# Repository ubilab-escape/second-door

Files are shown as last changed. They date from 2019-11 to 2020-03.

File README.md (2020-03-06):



**More notes on the implementation can be seen [here](
https://github.com/ubilab-escape/second-door/blob/master/docu/implementation.md)**

# Overview

- [Riddles](#Riddles)
  * [Stage 1 - Breaking the lock of the fusebox](#stage-1---breaking-the-lock-of-the-fusebox)
  * [Stage 2 - Restoring the power supply for the robot](#stage-2---restoring-the-power-supply-for-the-robot)
  * [Stage 3 - Breaking door by robot](#stage-3---breaking-door-by-robot)
- [Communication](#Communication)
- [How to](#How-to)
- [Future work](#future-work)

# Riddles

The main concept is visualized in the figure below.

<p align="center"> 
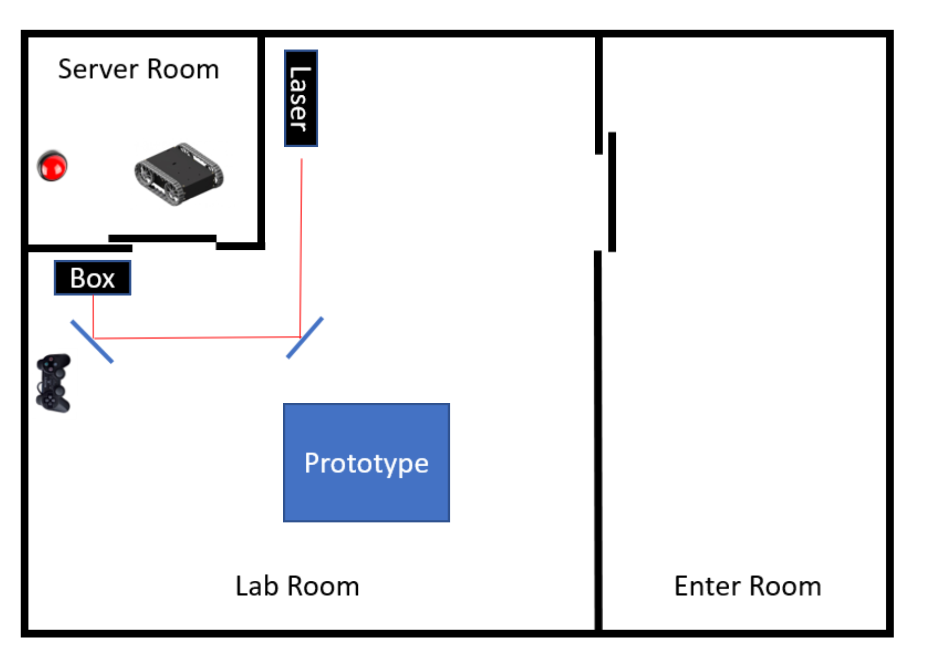
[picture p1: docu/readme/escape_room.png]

</p>
<p align="center">Figure 1: Main concept<p align="center">

To open the second door, 3 puzzles must be solved. These puzzles are called Stages in the following. In case the participants get stuck they can ask for hints. The implemented hints can be seen [here](/docu/hints.md)

## Stage 1 - Breaking the lock of the fusebox

In the first stage the group has to crack the lock of the fusebox. A laser somewhere in the room is to be used. There is a lock on the fusebox which can only be opened when the laser beam is aimed at it. To do this, the group must use mirrors to divert the laser beam through the entire room. The 2 mirrors that can be used are mounted on a wall. This hides them, and the group must come up with the idea of using the mirrors.

The lock on the fusebox measures the laser beam. So that only this specific laser light can open the lock. The readout of the signal is done by the ESP32 inside the fusebox. The progress of this crack process is visualized with LEDs arranged in a circle. Once this color circle is closed, the microcontroller gives a signal to an actuator so that the lid of the fusebox opens. This completes the first stage.

<p align="center"> 
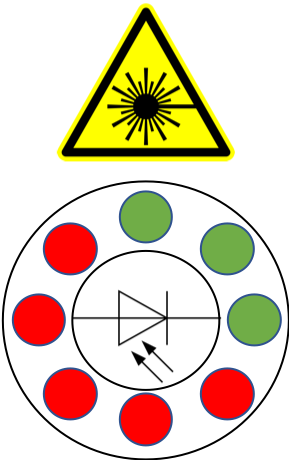
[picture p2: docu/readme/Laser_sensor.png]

</p>
<p align="center">Figure 2: Laser lock<p align="center">

To make it easier for the participants the laser warning symbol will be attached to the fusebox.

## Stage 2 - Restoring the power supply for the robot

Inside the fusebox two small "rewiring" riddles need to be solved . The following image shows the inside of the fusebox.

<p align="center"> 
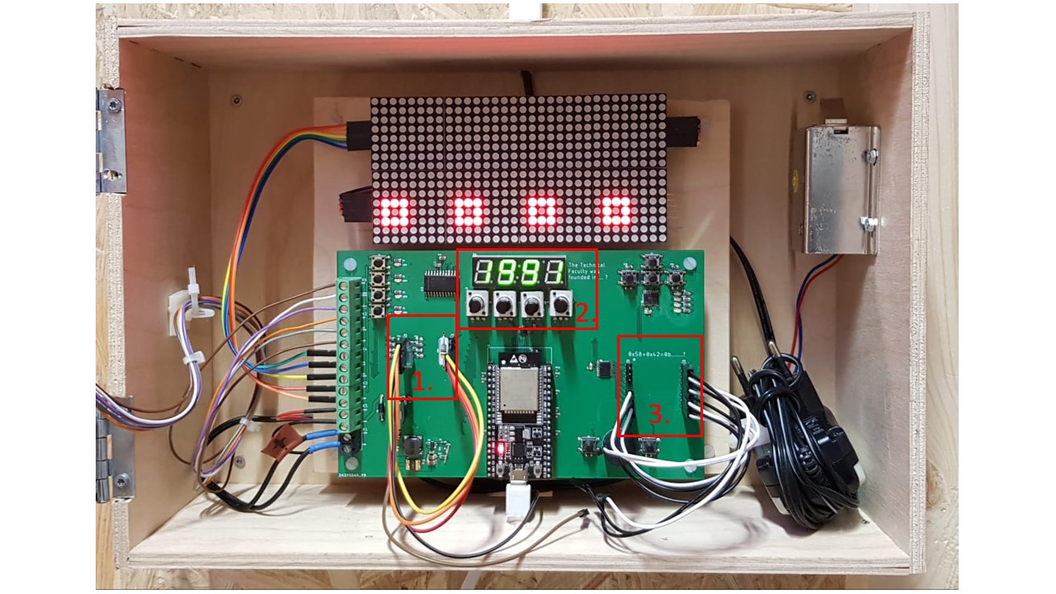
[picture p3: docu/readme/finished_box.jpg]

</p>
<p align="center">Figure 3: PCB fusebox<p align="center">

In the middle you can see an ESP32, which is responsible for the entire control of the PCB. Left to the ESP32, you can see two 5 pin headers (marked with 1). Both pairs must be connected using the attached jumper wire. The coding is hidden in the color marking of a soldered resistor which is right next to the connector. Above the ESP32 is a seven-segment display with 4 digits (marked with 2). With the help of potentiometers, a number can be set here (the year in which the faculty was founded). To the right of the ESP32 is the third riddle. Again the jumper wire needs to be connected in the right order. This time a binary number needs to be coded. Black wire indicates a zero and white wire a one. To get the right solution the participants have to sum up two hexadecimal numbers. The progress is visualized by an LED matrix on top of the PCB. In addition to the puzzles, there are other components on the PCB to confuse the group. When all the puzzles are solved, the robot inside the server room will get controllable from outside.

## Stage 3 - Breaking door by robot

It is just possible to open the door from inside by pushing a button with a small robot. Luckily the participants were able to repower the robot in the riddle before. The controller of the robot is placed on the other side of the room and a small window to look inside the server room is at the door. Therefore one participant has to guide the controlling one.

<p align="center"> 
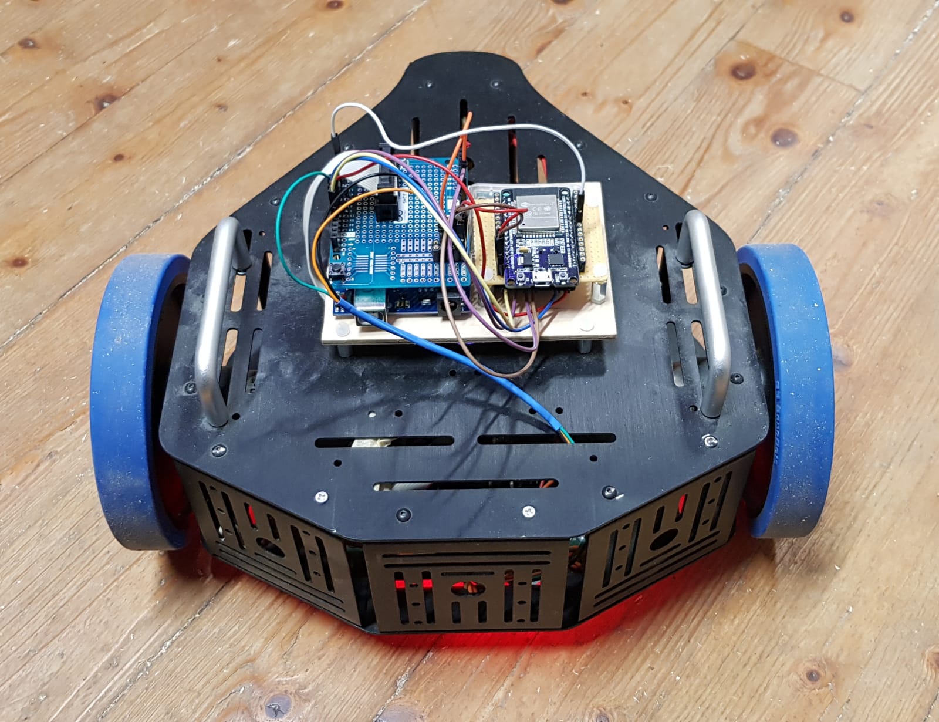
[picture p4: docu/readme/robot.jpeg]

</p>
<p align="center">Figure 4: Robot<p align="center">

# Communication

To standardize the communication for all devices and make the handling as easy as possible we implemented the [MqttBase](https://github.com/JayWiz/MqttBase). Each device for the above riddles make use of this class. The class is embedded as sub repository.

# How to

The project is structured in four folder:

| Folder 	| Description 	|
|---	|---|
[3D-files](https://github.com/ubilab-escape/second-door/tree/master/3D-files) | Contrains all .stp and .stl files for the designed cases |
[code](https://github.com/ubilab-escape/second-door/tree/master/code)| The .io files with all the code for each riddle |
[docu](https://github.com/ubilab-escape/second-door/tree/master/docu) | More detailed information about the implementation |
[pcb](https://github.com/ubilab-escape/second-door/tree/master/pcb) | The schematic and layout for the designed pcb |

The easiest way to work/compile/upload the code is to get [vs code](https://code.visualstudio.com/) and install [PlatfomIO](https://platformio.org/install/ide?install=vscode) as extension. The dependencies of each project are declared within the "lib_deps". The only missing part is the "wifi_secure.h" file which has to be created by the user. The file must contain:

```cpp
const char* ssid = "";
const char* password = "";
```

If you want to get the serial output for connection information define in the main.cpp file:

```cpp
#define DEBUG
```

# Future work

* robot controlled by ESP32 only
* cover/coating for pcb inside fusebox
* coating for fusebox

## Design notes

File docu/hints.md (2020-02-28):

# Laser

"Laser can destroy or open things"

"Light can be reflected"

"Look in the mirror"

"Redirect laser with mirrors"

# Fusebox

## Potentiometer

"One of the famous windows versions was released in this year"

"The last number is 5"

## Rewiring0

"Search for the biggest resistor"

"Look for matching colors"

"Color code indicates the right order"

## Rewiring1

"Add up values"

"Some numbers are binary"

"0x9A"

# Robot

"The door can just be opened from the inside"

"Push the button"

"Use the lighted robot"

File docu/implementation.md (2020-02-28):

# Implementaion

In this file we are going to show and document the main implementation tasks. [Here](https://github.com/ubilab-escape/second-door/projects/2) you can see the project progress and the issues we worked on.

# General

The communication structure for all devices is listed in the figure below. 
<p align="center"> 
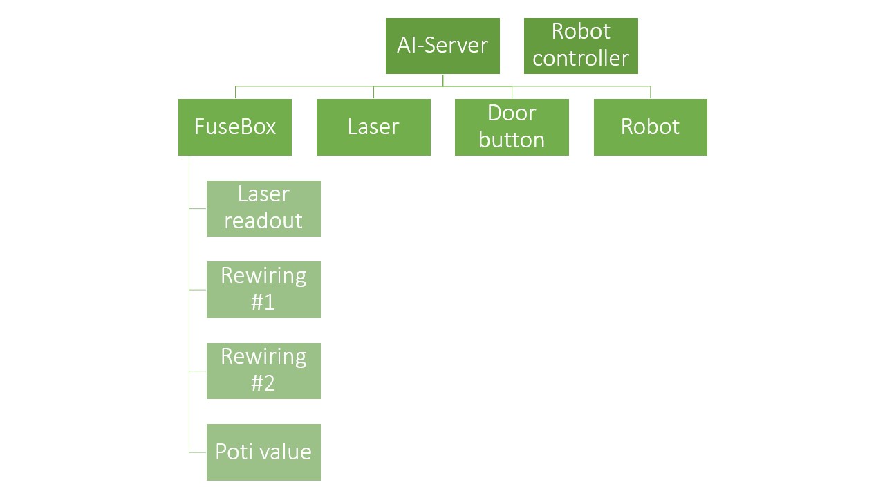
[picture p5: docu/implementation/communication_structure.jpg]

</p>
<p align="center">Figure 1: Visualization for the communication structure<p align="center">

As you can see, all devices communicate with the server, except the controller.

# Fuse Box
The design of the fusebox is visualized in the following figure.
<p align="center"> 
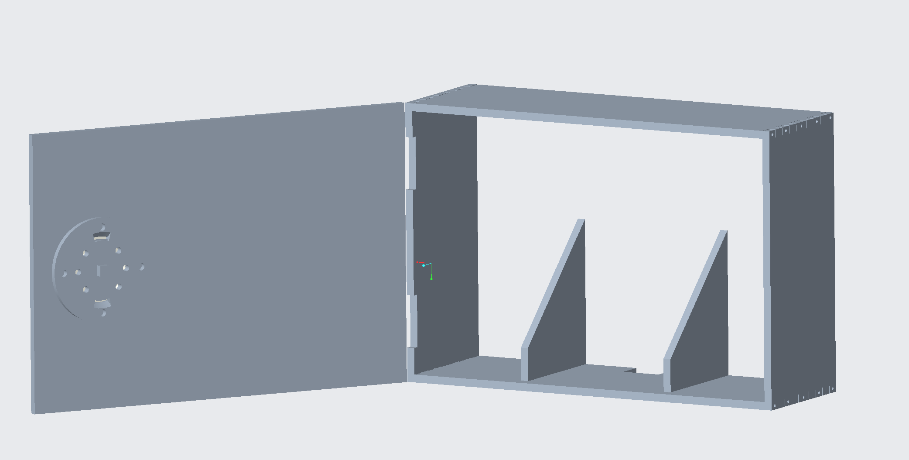
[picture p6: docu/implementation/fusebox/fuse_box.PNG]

</p>
<p align="center">Figure 2: Design fuse box<p align="center">

## PCB

In the following images, you can see the schematics of the fusebox. Page 1 shows the connections between ESP32 and all logic signals. The power supply, which is on page 2, converts 12V DC to 5V @ 3A. Connections to mechanical and optical parts of the PCB, e.g. potentiometers, pinheader, leds, buttons and piezobuzzer. The circuit of the seven segment display, which shows the setting of the potentiometers, can be seen in page 4. We used a MAX7221, a serially interfaced (SPI) 8 bit current sink, which is often used as led driver. On page 5, connections to screw terminal blocks are shown. With those, one can connect external peripheral elements to the PCB. Finally, on page 6 you can see the circuit of I2C components. We used two PCF8574 8 bit I2C I/O port expanders, and one ADS1015 12 bit 4 channel delta-sigma I2C ADC. Both port expanders are used for additional peripheral elements, e.g. readout of second rewiring puzzle, readout of additional buttons and driving some leds. An external ADC was necessary, since we couldn't use some internal ADC pins of the ESP32, because they could influence boot options on startup in case they are connected to our potentiometers.

<p align="center">
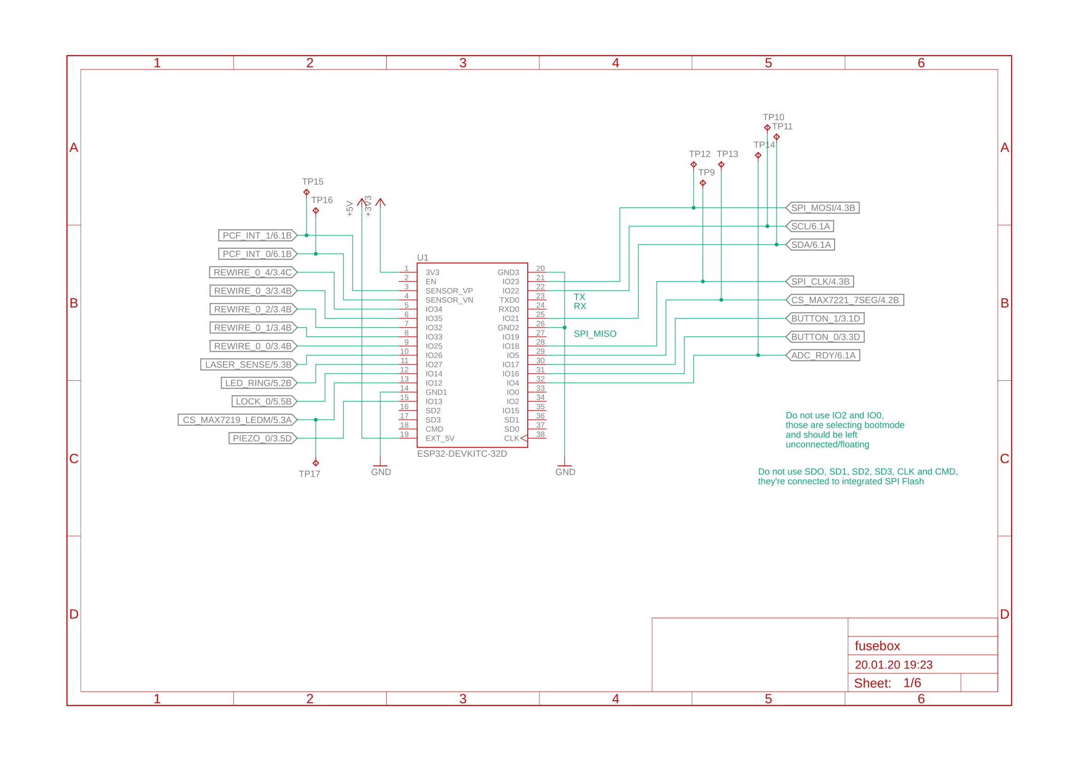
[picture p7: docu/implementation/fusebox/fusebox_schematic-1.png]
  
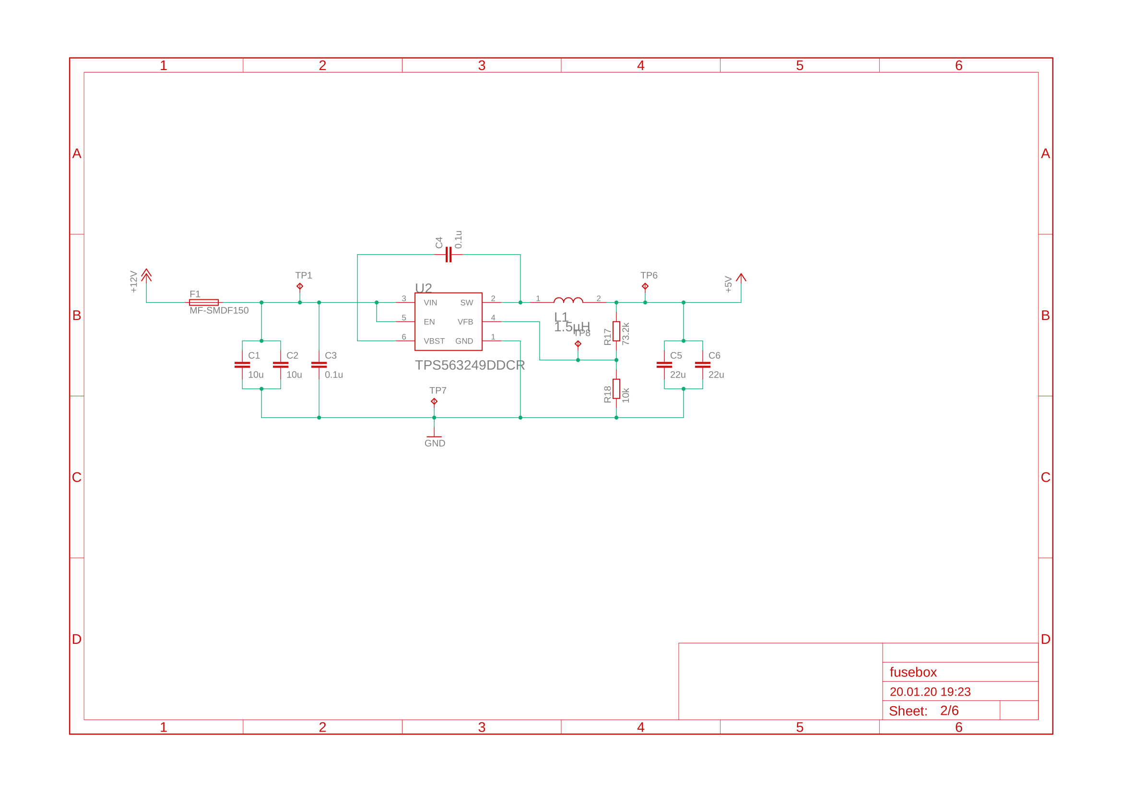
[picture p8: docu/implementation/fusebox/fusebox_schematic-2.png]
  
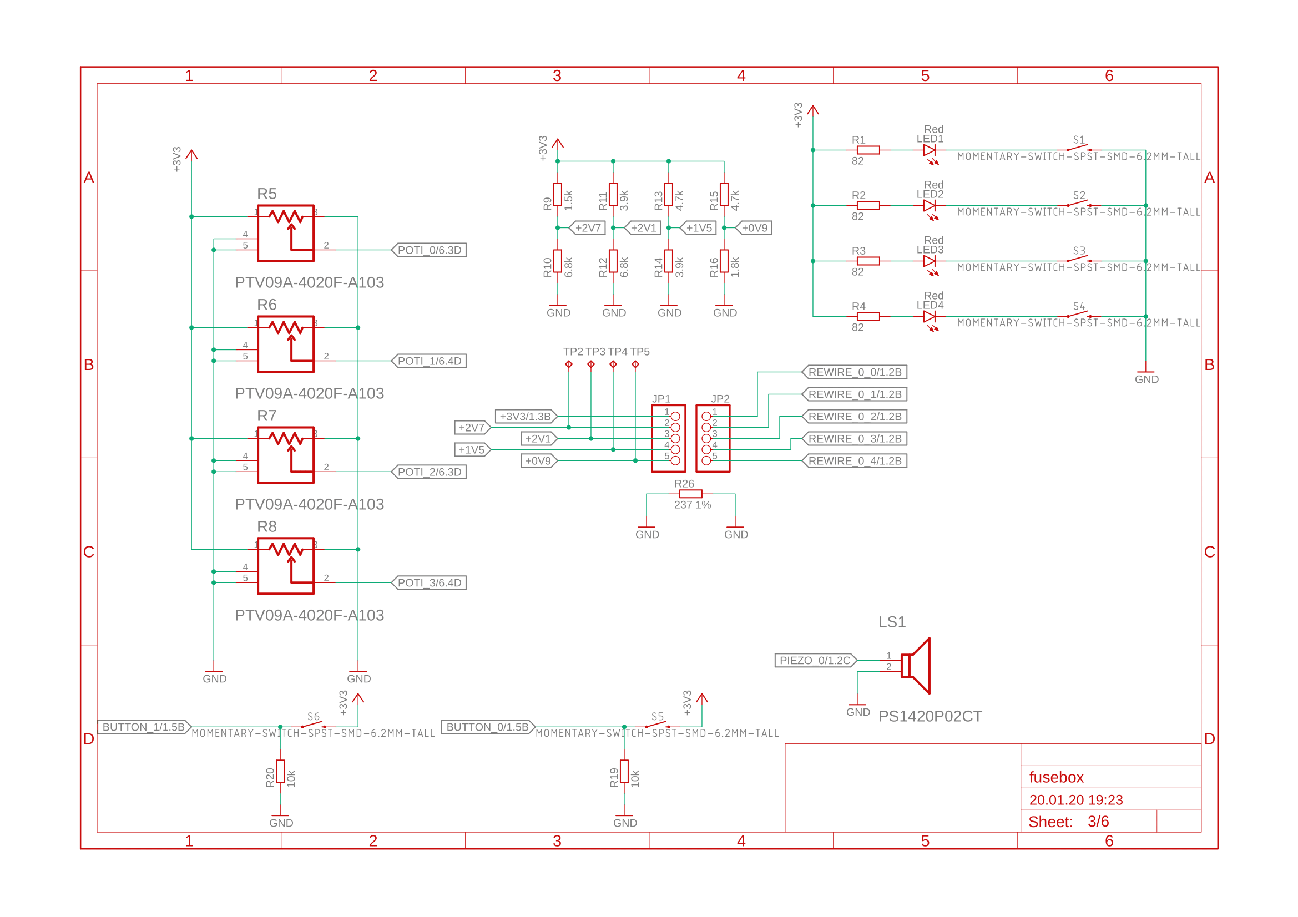
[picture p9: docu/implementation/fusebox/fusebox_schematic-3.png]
  
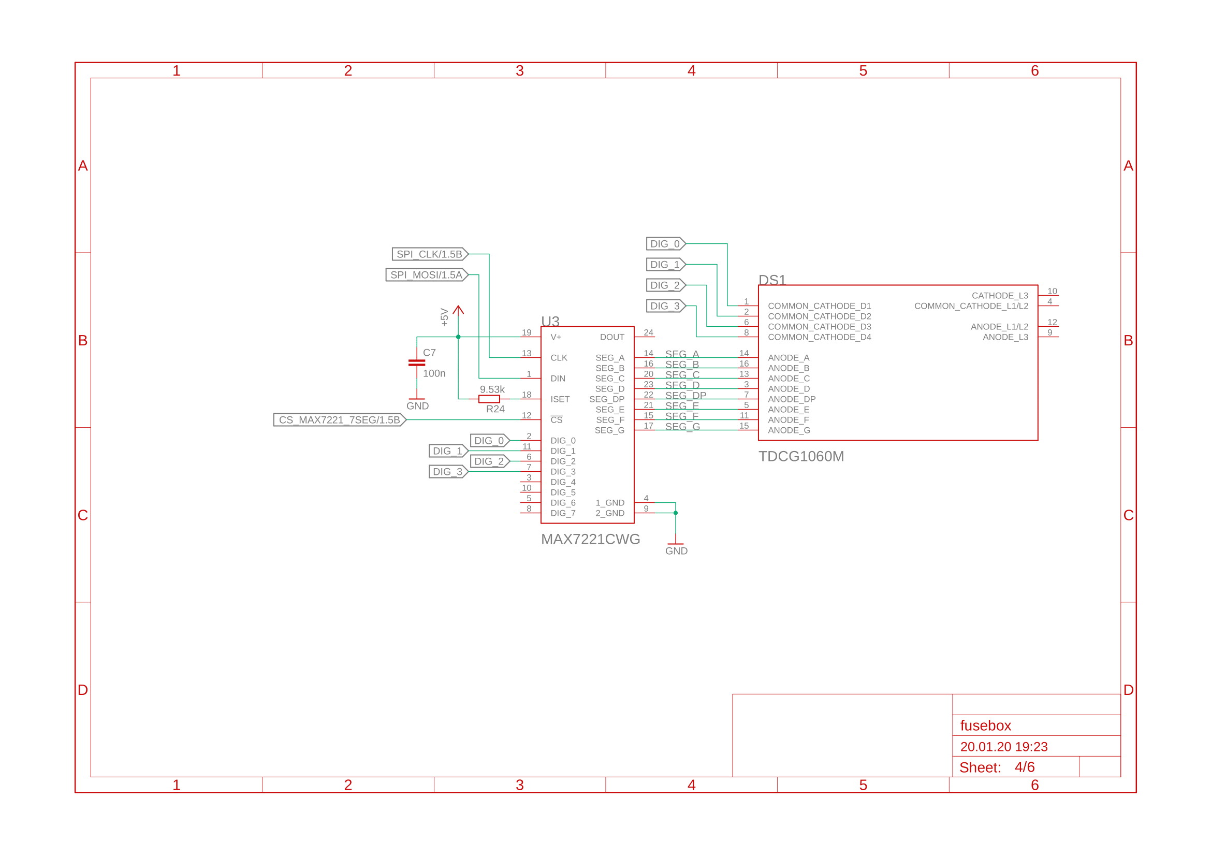
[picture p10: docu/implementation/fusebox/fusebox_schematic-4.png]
  
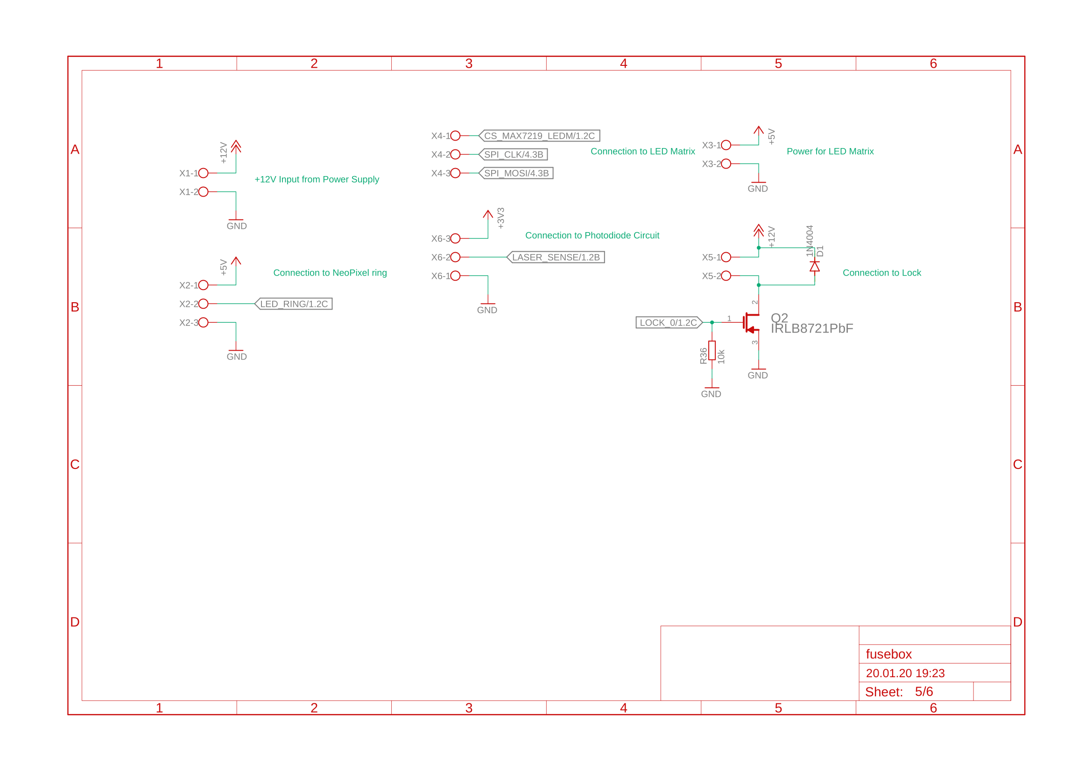
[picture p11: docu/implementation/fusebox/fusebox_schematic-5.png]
  
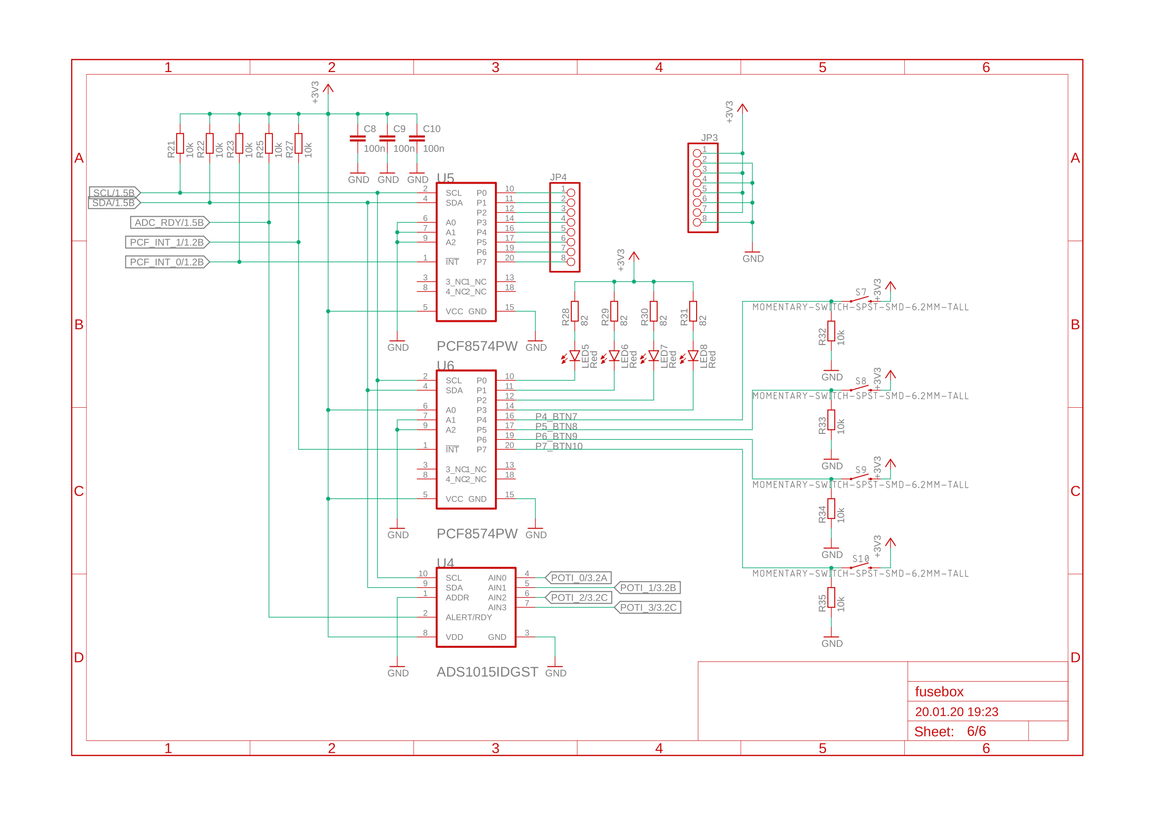
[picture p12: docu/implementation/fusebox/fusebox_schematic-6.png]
  
</p>
<p align="center">
  Figure 3: schematics of fusebox pcb
</p>

The shown schematic was used to design the pcb, pictured in figure XX. Initally, a 4 layer setup should be used, but to keep the price low, we decided to use a 2 layer setup, at the expense of signal quality. Reducing the number of layers was still possible, since we designed the PCB very forsighted (top/vertical and bottom/horizontal layer should have been used for signals, 2 and 15 for GND and power). The shown design contains both mounting techniques (SMD and THT), preferred package size is 0805. We ordered prototypes of this PCB at JLC PCB in China, the delivered pcbs were fully functional. After manually soldering all parts to pcb, we tested and programmed all functionality. Apart from 1 badly designed pad, everything worked fine and the board is fully functional.  

<p align="center">
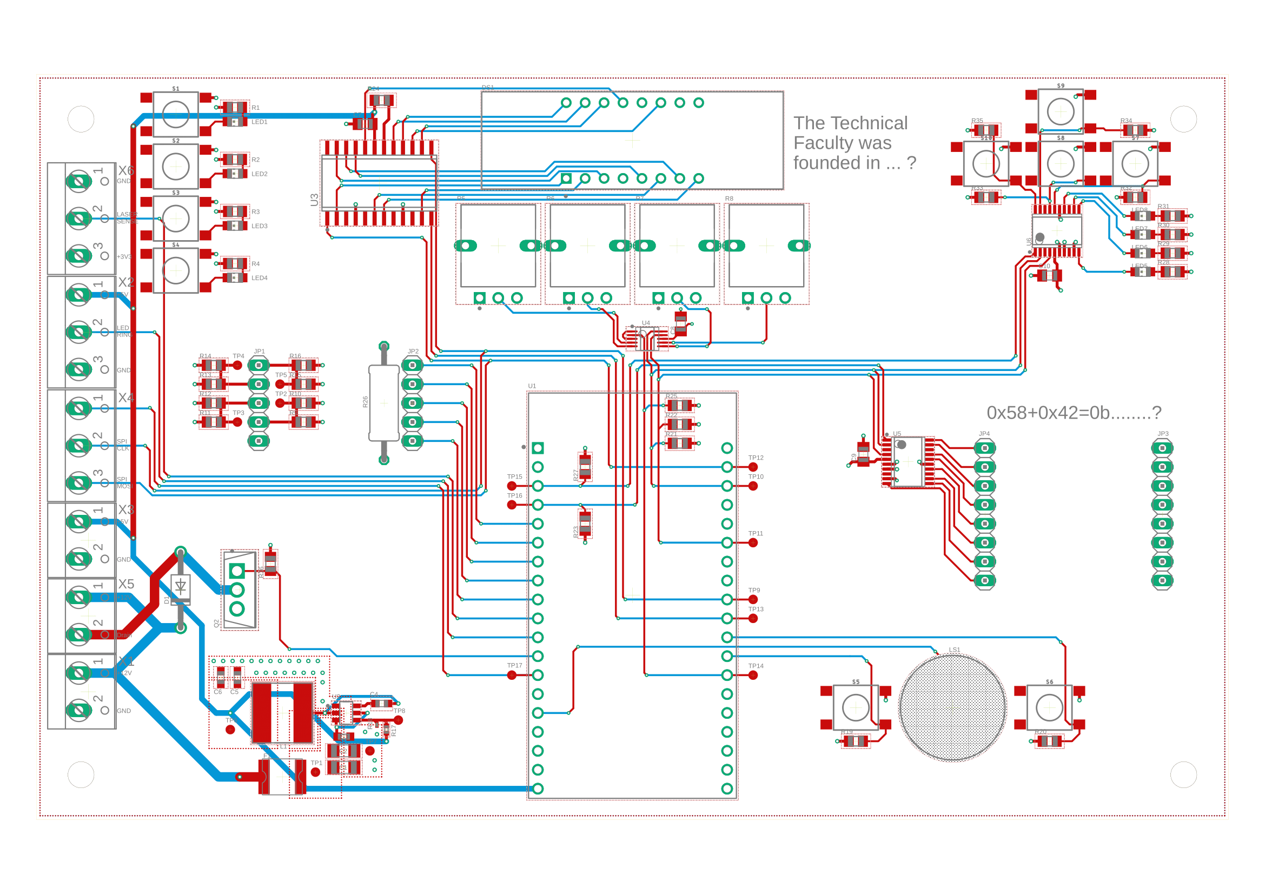
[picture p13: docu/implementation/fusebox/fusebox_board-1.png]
  
</p>
<p align="center">
  Figure 4: design of fusebox pcb
</p>

The assembled, mounted and connected pcb is shown in figure XX.

## Door

The laser is used to melt the lock. [LED ring](https://www.adafruit.com/product/2855) is used to indicate the status. 

<p align="center"> 
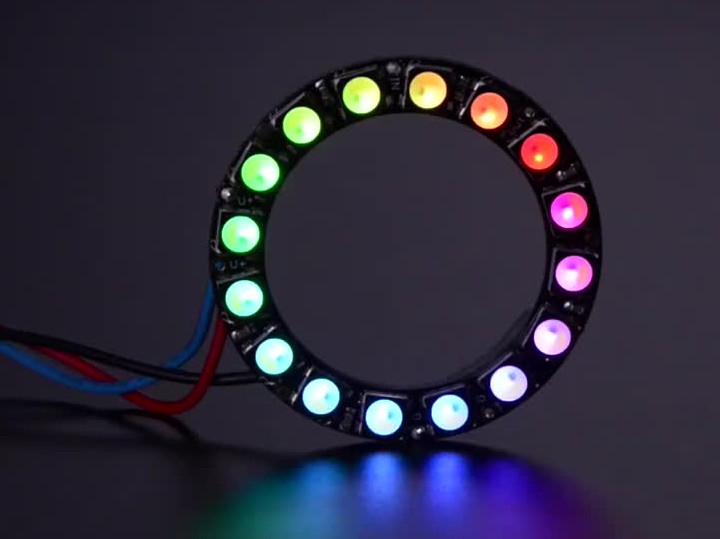
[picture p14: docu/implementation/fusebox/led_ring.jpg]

</p>
<p align="center">Figure 5: LEDs for indicating status of melting lock process<p align="center">
  
The laser beam is diverted by the mirrors and hits the detector visible below. The detector is equipped with a photodiode and an integrated comparator, which outputs a logical one when it detects a laser beam. The high response time of the diode allows to modulate a frequency to the laser and to detect this. The frequency is needed to prevent the puzzle from being bypassed by a flashlight. The signal is passed to an input of the ESP32 and this is sampled. A sequence of six samples is stored and checked for the equivalent number and order of zeros and ones. If this is given, the first LED of the ring is set to green. This is repeated until all sixteen LED's are green. Then the LED ring flashes three times to signal that the puzzle is solved. To increase the difficulty, a green LED is set to red again after one second to increase the difficulty.

<p align="center"> 
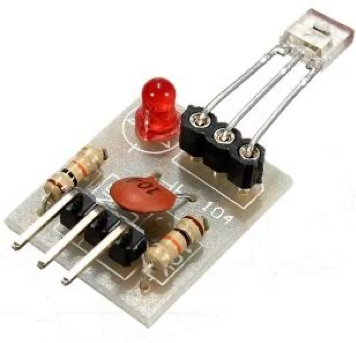
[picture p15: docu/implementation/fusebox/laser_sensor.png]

</p>
<p align="center">Figure 6: Sensor to detect the laser beam<p align="center">

# Laser + Box

[Laser](https://www.adafruit.com/product/1054) 

The white circle shown in the figure below is lighted with LEDs. This is going to be used to get the attention of the participants.

<p align="center"> 
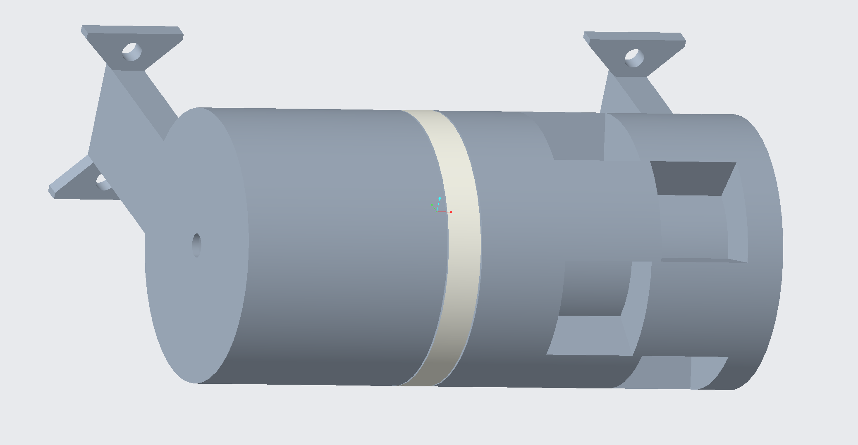
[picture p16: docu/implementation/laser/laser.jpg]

</p>
<p align="center">Figure 7: Case for laserdiode<p align="center">

Inside the laser there is an ESP32 which controls the laser by means of PWM. The line to the laser is interrupted by a button that must be pressed to switch on the laser. For the control of the LEDs the neopixel library from Adafruit is used. Switching on is done via communication. In the "off" state, neither the laser can be activated via the button nor the LEDs are switched off. In "on" state the LED ring is set to red and the PWM is connected to the pin of the ESP32.

# Button to open door

Inside the laser is an ESP32. If it receives "trigger" "on" the button lights up. If it receives "trigger" "off" the button goes out. If the button is pressed, "solved" is sent and the button will look until it receives a "trigger" "off".

<p align="center"> 
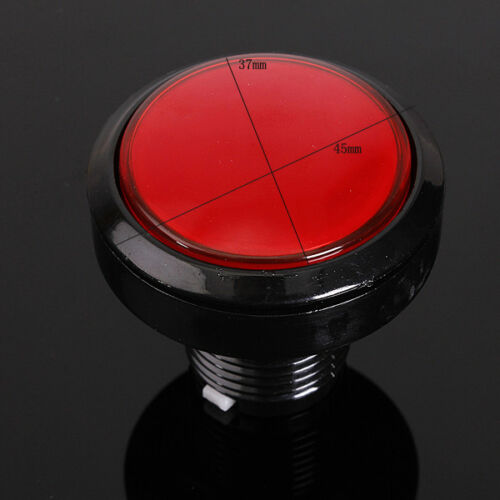
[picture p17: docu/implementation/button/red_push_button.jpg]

</p>
<p align="center">Figure 8: Push button to open the door inside the server room<p align="center">

# Cat flap

Not decided yet!

**Problem**: sliding door does not allow much space for stepper/linear track/..

Possible solutions:

* FuseBox switches on the light inside the server room -> now robot can be seen inside the room
* usual cat flap with small lock

# Robot with controller

The robot will be controlled with an wireless PS2 controller which is attached to the wall. There exists a [library](http://www.billporter.info/2010/06/05/playstation-2-controller-arduino-library-v1-0/) to read out the commands.

<p align="center">
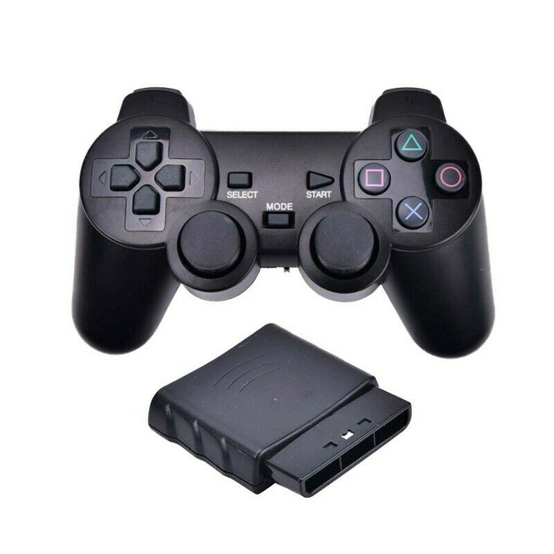
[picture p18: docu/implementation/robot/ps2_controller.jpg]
  
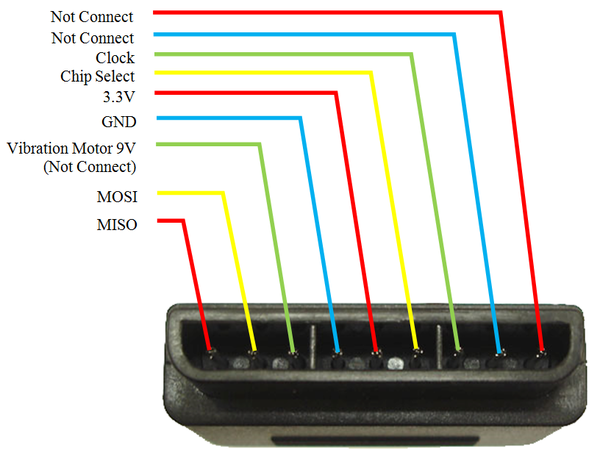
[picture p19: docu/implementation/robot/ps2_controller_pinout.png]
   
</p>

<p align="center">Figure 9: PS2 controller wireless with pinout<p align="center">

As chassis for the robot an old prototype from the university is used. There is already some electronic to controll the two dc-motors.

<p align="center"> 
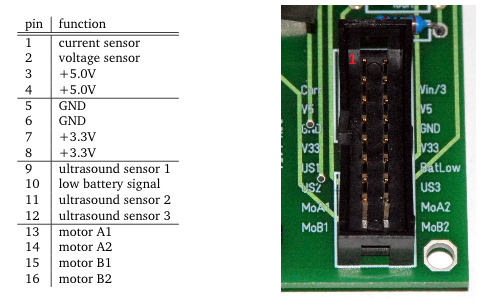
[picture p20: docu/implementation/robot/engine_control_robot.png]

</p>
<p align="center">Figure 10: Pinout for existing robot electronic<p align="center">

The pins "motor A1" and "motor A2" are used to controll the left wheel of the robot. Pins "motor B1" and "motor B2" for the right wheel. A LED is used to visualize if the battery of the robot is low. Furthermore there are LEDs "arround" the robot to attract attention of the participants.

<p align="center"> 

</p>
<p align="center">Figure 11: Robot with LEDs<p align="center">

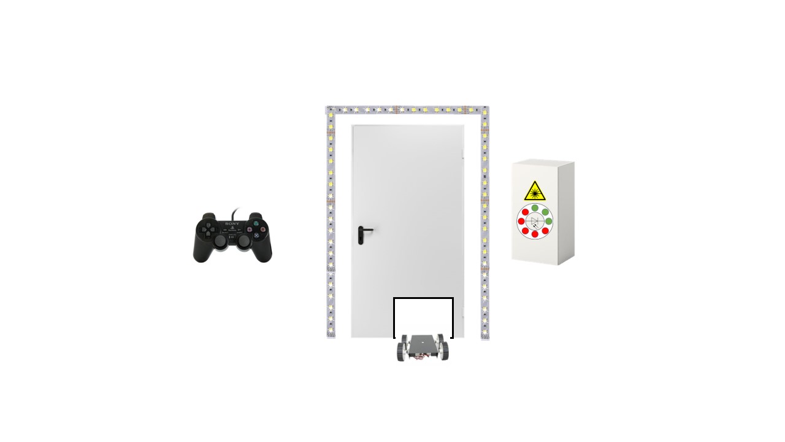
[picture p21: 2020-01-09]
docu/readme/second_door_main_concept.jpg

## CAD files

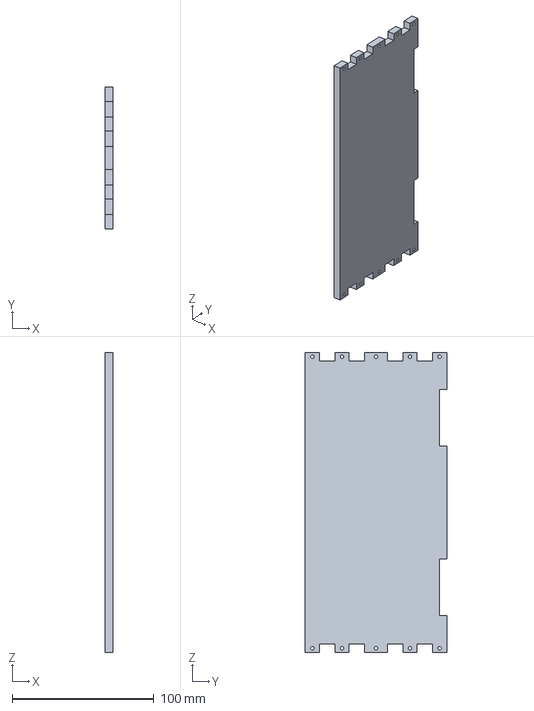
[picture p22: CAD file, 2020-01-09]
3D-files/fuseBox/fuse_box_side_left.stp
6.00 x 100.0 x 212.0 mm

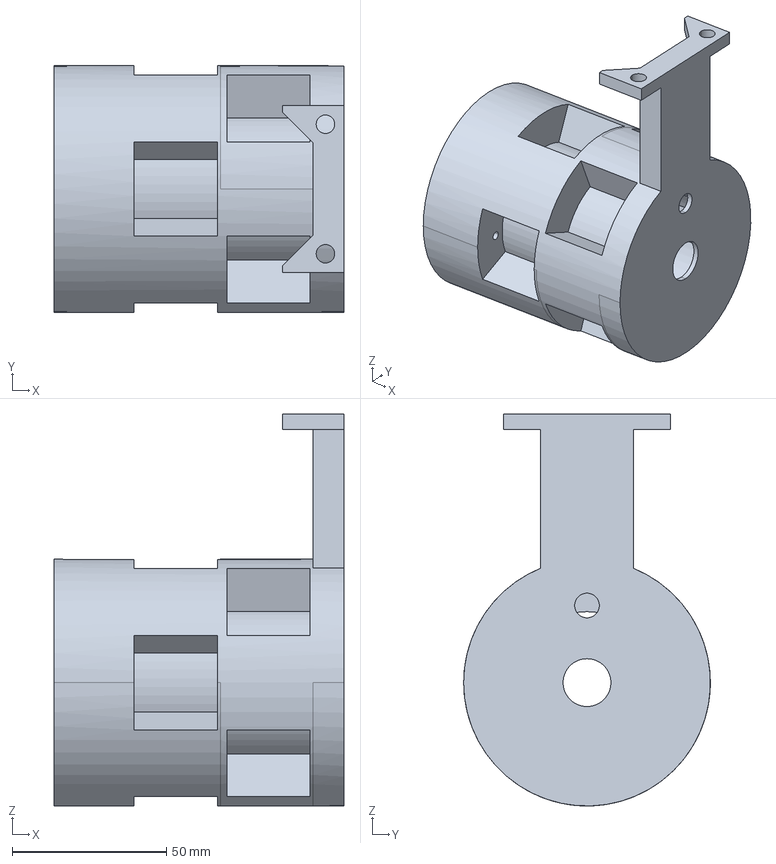
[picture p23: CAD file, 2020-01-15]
3D-files/laserCase/top.stp
94.0 x 80.0 x 127.1 mm

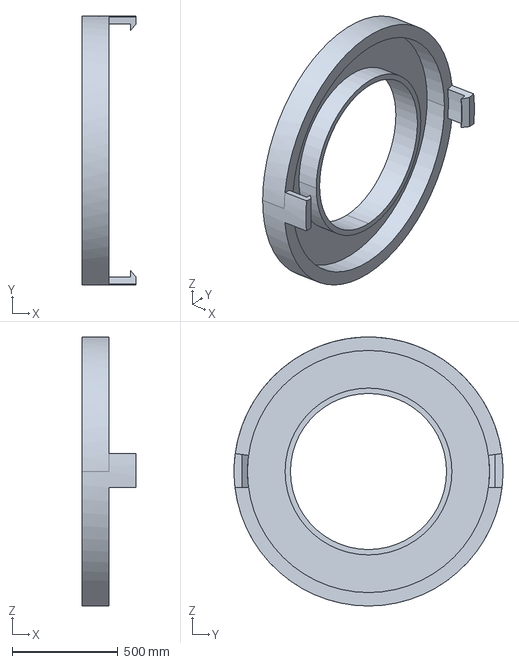
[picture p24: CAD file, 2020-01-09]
3D-files/LEDRing/led_ring_cover.stp
254.0 x 1270.0 x 1270.0 mm

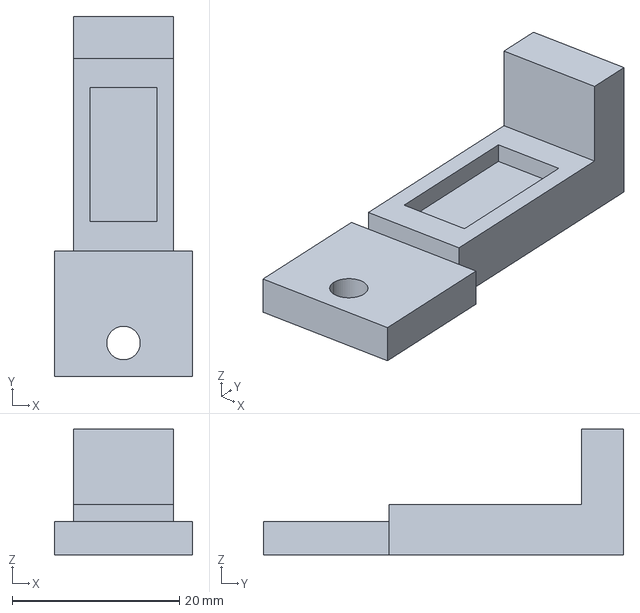
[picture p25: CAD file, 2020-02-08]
3D-files/PS2mount/mount_fix.stp
16.5 x 43.0 x 15.0 mm

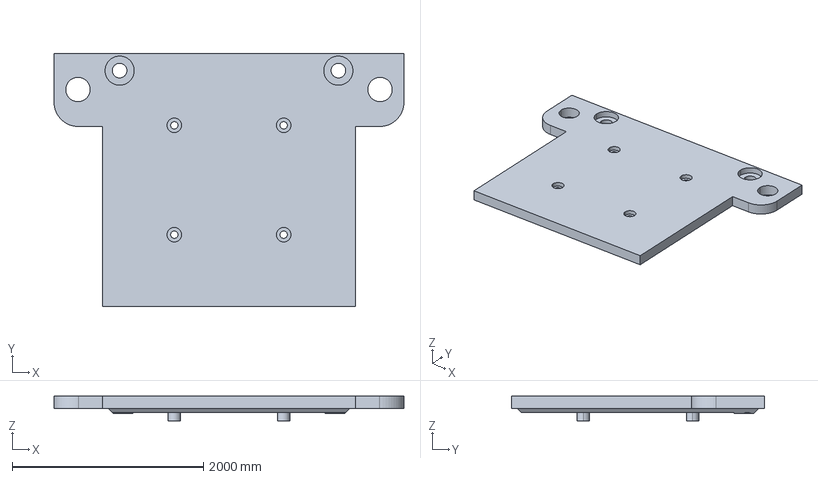
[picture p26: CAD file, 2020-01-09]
3D-files/pushButton/push_button_case_button.stp
3657.6 x 2641.6 x 258.6 mm

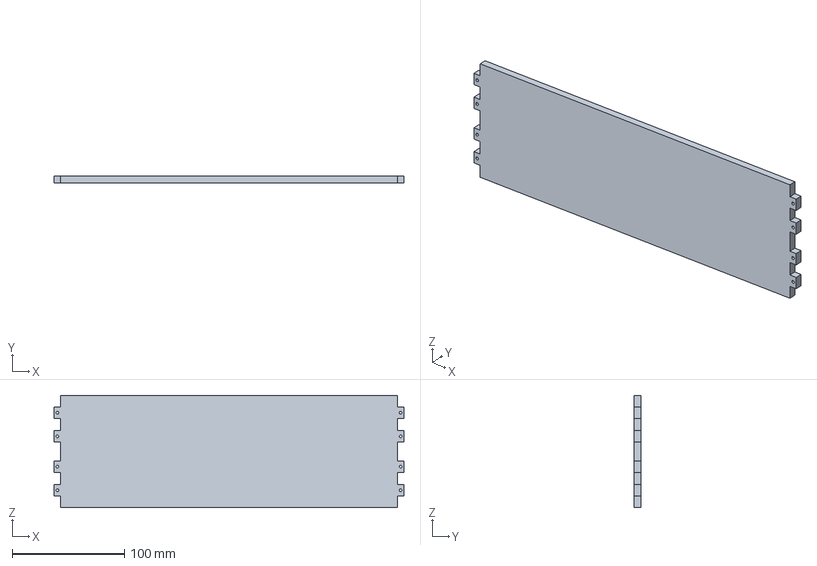
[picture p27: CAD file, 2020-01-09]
3D-files/fuseBox/fuse_box_top.stp
312.0 x 6.00 x 100.0 mm

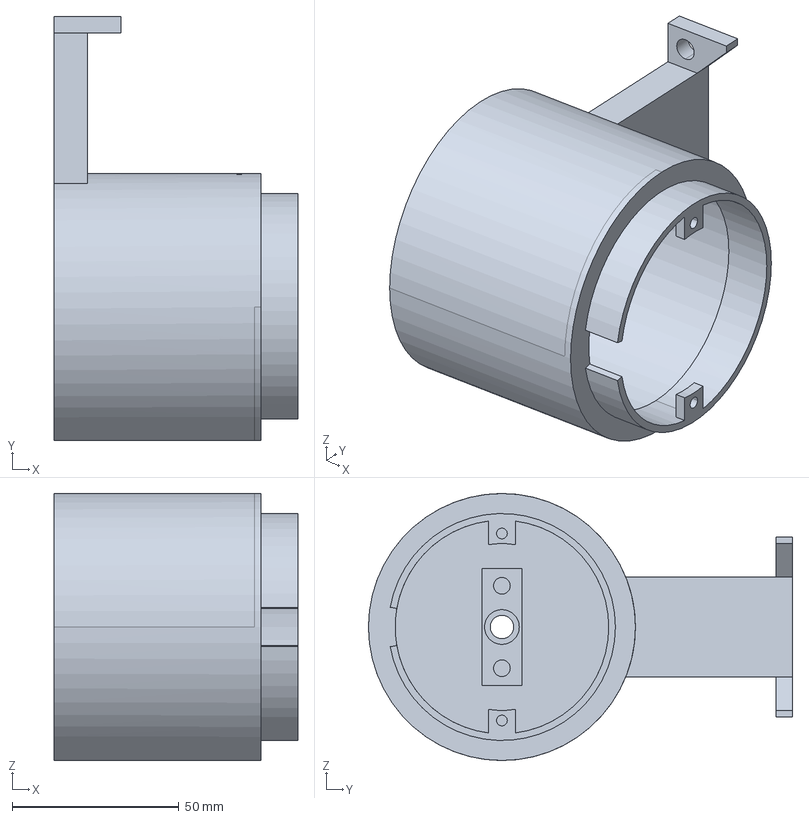
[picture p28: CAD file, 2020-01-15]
3D-files/laserCase/bottom.stp
73.0 x 127.1 x 80.0 mm

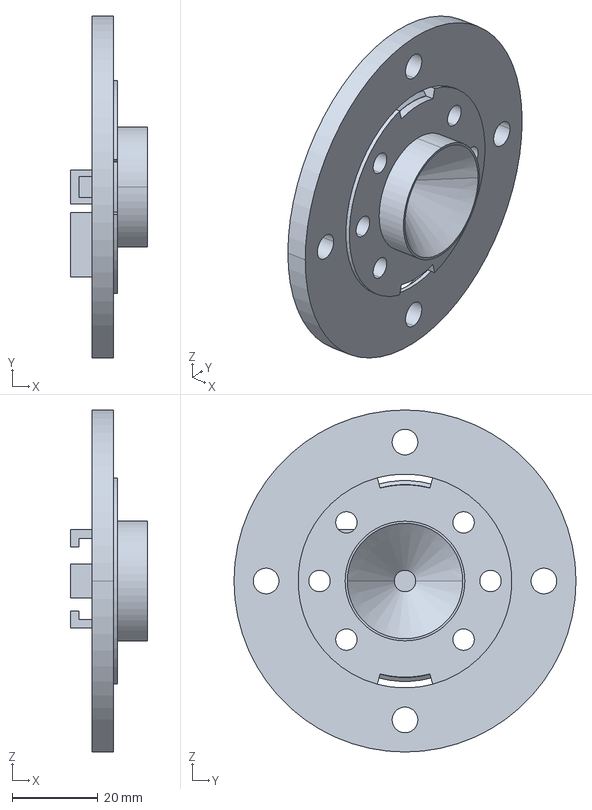
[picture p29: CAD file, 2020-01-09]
3D-files/LEDRing/led_ring_mount.stp
18.0 x 80.0 x 80.0 mm

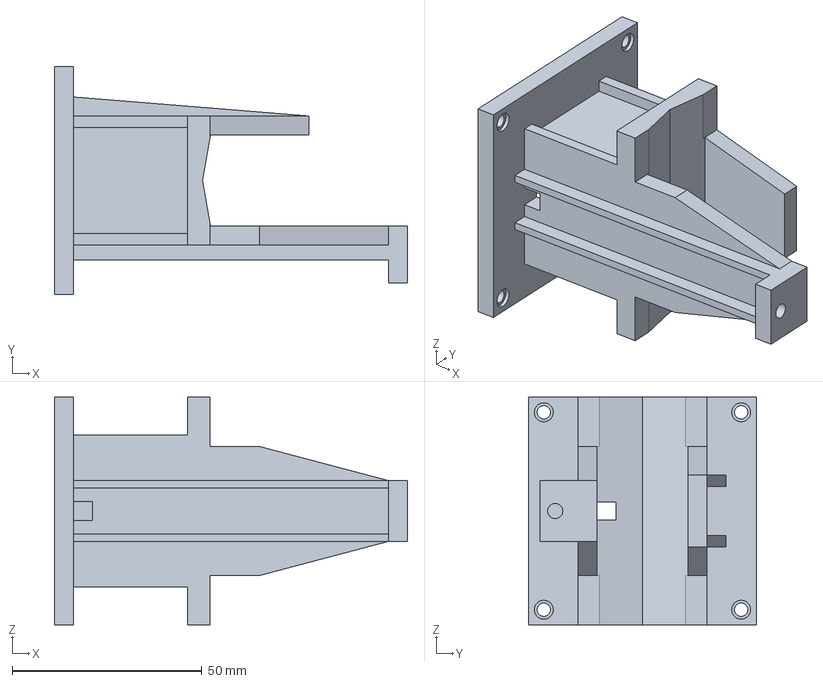
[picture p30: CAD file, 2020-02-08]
3D-files/PS2mount/wall_mount.stp
93.0 x 60.0 x 60.0 mm

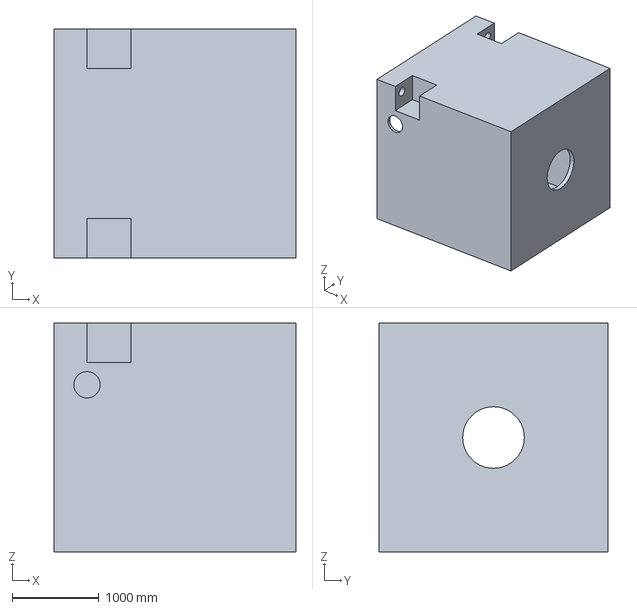
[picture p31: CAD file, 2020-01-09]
3D-files/pushButton/push_button_case_top.stp
2794.0 x 2641.6 x 2641.6 mm

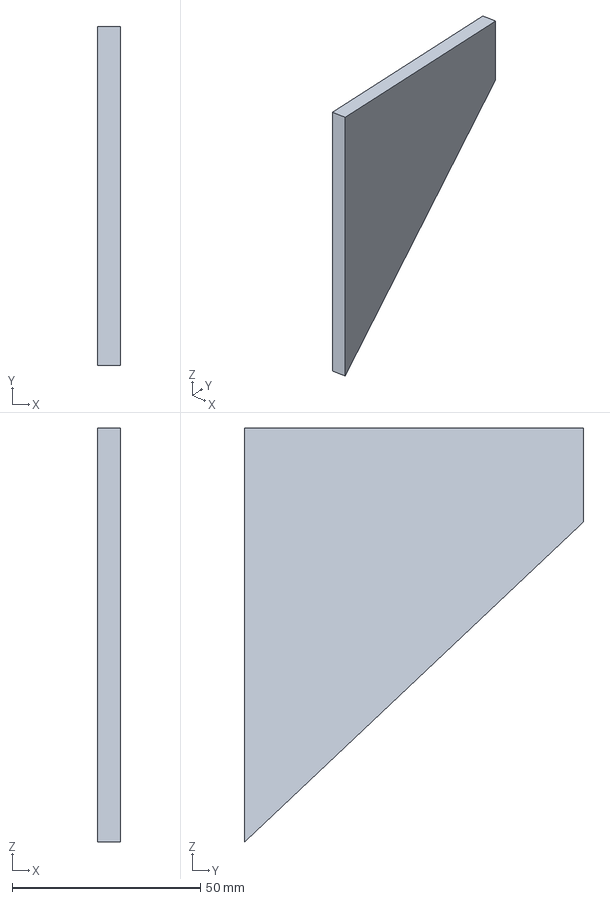
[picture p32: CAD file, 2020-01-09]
3D-files/fuseBox/pcb_holder.stp
6.00 x 90.0 x 110.0 mm

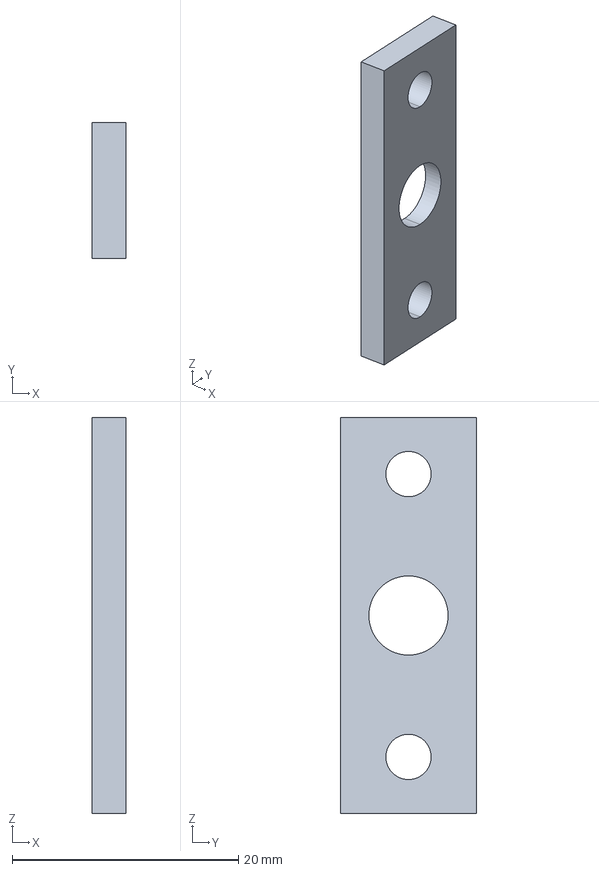
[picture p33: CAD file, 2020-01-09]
3D-files/laserCase/laser_lock.stp
3.00 x 12.0 x 35.0 mm

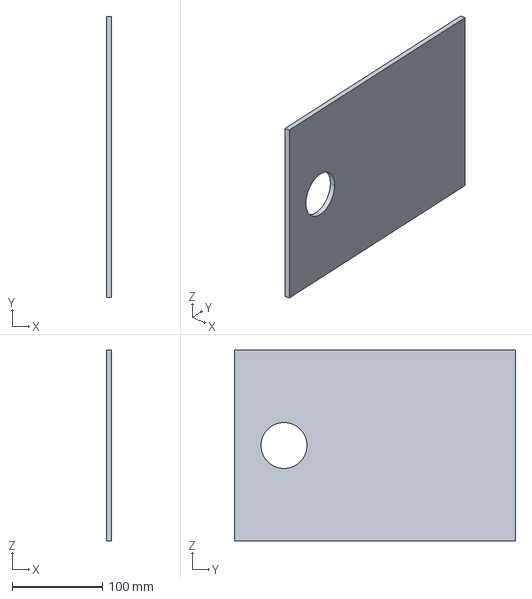
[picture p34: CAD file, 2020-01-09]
3D-files/fuseBox/fuse_box_door.stp
6.00 x 312.0 x 212.0 mm

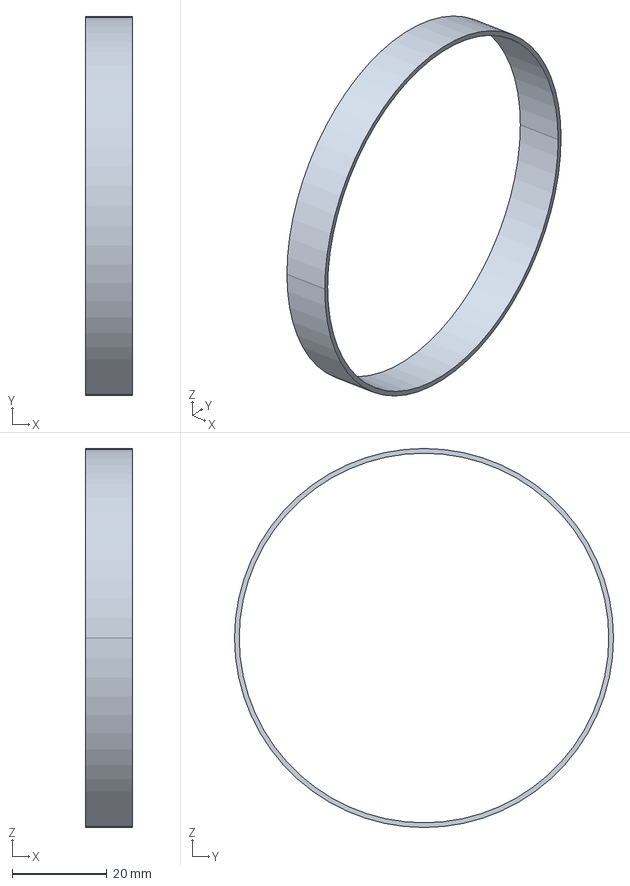
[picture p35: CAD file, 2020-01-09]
3D-files/laserCase/ring.stp
10.0 x 80.0 x 80.0 mm

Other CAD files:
3D-files/fuseBox/fuse_box_bottom.stp
3D-files/fuseBox/fuse_box_side.stp
3D-files/LEDRing/led_ring_cover.stl
3D-files/LEDRing/led_ring_mount.stl
3D-files/PS2mount/mount_fix.stl
3D-files/PS2mount/wall_mount.stl
3D-files/laserCase/bottom.stl
3D-files/laserCase/laser_lock.stl
3D-files/laserCase/ring.stl
3D-files/laserCase/top.stl
3D-files/pushButton/push_button_case_button.stl
3D-files/pushButton/push_button_case_top.stl

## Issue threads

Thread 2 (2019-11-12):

proof of concept - hardware

JayWiz, 2019-11-12:
Implement a proof of concept for the hardware. This should include:

- [x] first sketch of schematic

- [x] realization of basic functions on breadboard

- [x] bill of materials for needed hardware

JayWiz, 2019-11-22:
Already started with the realization of basic functions on breadboard. Still waiting for some ordered materials.

JayWiz, 2019-12-20:
is done

Closed 2019-12-20.

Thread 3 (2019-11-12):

proof of concept - software

JayWiz, 2019-11-12:
Implement a proof of concept for the software. This should include:

- [x] control and read different components on PCB (LEDs, 7-Segment, potentiometers, buttons, etc.)

- [ ] basic communication with AI server or local raspberry instance

JayWiz, 2019-11-22:
Started with proof of concept of software. already implemented various functions.

JayWiz, 2019-11-28:
Finished proof of concept - software, see #13

Closed 2019-11-28.

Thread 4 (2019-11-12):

design - hardware

JayWiz, 2019-11-12:
Design the hardware for the fusebox:

- [x] schematics and design of PCB

- [x] BOM (bill of materials)

- [x] gerber files of PCB design

- [ ] documentation

JayWiz, 2019-11-22:
Started with design of schematic in EAGLE.

JayWiz, 2019-11-25:
todo list:

- [ ] add fuses to power part

- [ ] figure out how to use the MAX7219/MAX7221, and connect it properly to the SPI pins of the ESP32 (also: DOT matrix)

- [ ] connect color sensor / photodiode to I2C bus, add pull ups on I2C bus and reserve I/O pin for interrupt (analog port, 2 I2C and interrupt)

- [ ] connect led stripe of laser lock to I/O port of ESP32

- [ ] drive mosfet with I/O pin from ESP32

JayWiz, 2019-11-25:
Features to implement:

- [ ] 4 buttons in the corners of the pcb
- [ ] potentiometer with various LEDs around
- [ ] ...

JayWiz, 2019-11-27:
POTI PINS CHANGED!!!

JayWiz, 2019-12-20:
everything is done, PCB is ordered.
parts of the bom have to be ordered

JayWiz, 2019-12-20:
documentation should be done and written to README

JayWiz, 2020-01-17:
Hardware is completely done, documentation still missing, but is mentioned in other issue

Closed 2020-01-17.

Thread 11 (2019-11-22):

proof of concept - laser puzzle

TKoe92, 2019-11-22:
test multiple variants to detect the laser beam

TKoe92, 2019-11-22:
tested RGB Sensor: robust detection of red laser beam. The small sensor has to be hidden very precisely....
tested reverse diode: Measured Voltage drop was 0.075V. Not enough for and not robust enough-> do not use this methode

TKoe92, 2019-12-04:
tested LDR: pulse the laser to avoid opening the fusebox with flashlight. Therefore tried to use timer interrupts to measure the value over the LDR every ms. Problem, the LDR needs to much time to recover to its initial state....
also tested an Interrupt generated by a gpio. This is only possible as pullup and detect an falling or rising flag. Therefor an additional circuit would be needed.
To avoid that a second test with the RGB sensor was done. With more distance the laser beam scatters and it is easer to hit the small sensor. The red laser beam if measurable even though the led ring is illuminated red!

TKoe92, 2019-12-09:
use laser sensorn now! The laser pointer is pulses with 50 Hz. It is not possible to unlock the the box with a flashligth. The sensor is much more sensitiv and easier to hit with the laser beam

Closed 2019-12-11.

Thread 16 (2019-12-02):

Noise on Buzzer while using LEDmatrix

JayWiz, 2019-12-02:
Maybe implement a bandpass filter

JayWiz, 2020-01-17:
still a problem, even on new hardware. not that important, but still annoying

JayWiz, 2020-01-30:
no idea how to solve this problem, cannot change it

Closed 2020-01-30.

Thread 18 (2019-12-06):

Add second PCF8574 to Design

JayWiz, 2019-12-06:
More GPIOs for additional functions, e.g. buttons to control or interact with the LedMatrix.

JayWiz, 2019-12-06:
Due to the fact, that there will be multiple partcipants on the I2C bus, and there are also long wire lengths, series and pullup resistors should be added to the I2C bus!

JayWiz, 2019-12-09:
Done, see 68b4eb4046f455ff02757d2a2ea7bfa274021502

Closed 2019-12-09.

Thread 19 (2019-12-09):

IO 15, 2, 0, 4 causing boot problems

JayWiz, 2019-12-09:
Potentiometers connected to IO pins 15, 2, 0, 4 can cause problems during boot. (see https://randomnerdtutorials.com/esp32-pinout-reference-gpios/)

JayWiz, 2019-12-09:
https://github.com/espressif/esptool/wiki/ESP32-Boot-Mode-Selection

JayWiz, 2019-12-11:
Added additional ADC, therefore pins 2 and 0 are not used anymore. Pins 15 and 4 are used as GPIOs (Input)

Closed 2019-12-11.

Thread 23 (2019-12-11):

add cheap ics, leds and resistors with no function to pcb

JayWiz, 2019-12-11:

JayWiz, 2019-12-18:
didn't add any, theres already enough stuff on the pcb

Closed 2019-12-18.

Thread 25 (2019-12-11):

MQTT communication

TKoe92, 2019-12-11:
Communicate with the Operator:

- [x] setup WiFi

- [x] setup MQTT

- [x] define global Variables for each puzzle and implement them to skip puzzles if necessary

- [x] draw flow chart for operator group

- [x] setup topics and tx/rx messages

JayWiz, 2020-01-17:
MQTT still missing entirely for fusebox

JayWiz, 2020-01-17:
SequenceWorkflow("Solve fusebox", [
                    ActivateLaserWorkflow("Laser_lab_room", "7/laser"),
                    Workflow("Fusebox_lab_room", "7/fusebox/laserDetection"),
                    ParallelWorkflow("Solve fuse box", [
                        Workflow("Fusebox_lab_room", "7/fusebox/rewiring0"),
                        Workflow("Fusebox_lab_room", "7/fusebox/rewiring1"),
                        Workflow("Fusebox_lab_room", "7/fusebox/potentiometer")
                    ]),
                    Workflow("Robot_lab_room", "7/robot")
                ])

TKoe92, 2020-01-23:
use mqtt_base subrepo for communication

Closed 2020-01-23.

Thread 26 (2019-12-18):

Replace MOSFET by darlington

JayWiz, 2019-12-18:
https://cdn-shop.adafruit.com/product-files/412/solenoid_driver.pdf

JayWiz, 2019-12-18:
Replaced with other MOSFET with lower gate source voltage: https://datasheet.octopart.com/IRLB8721PBF-Infineon-datasheet-8326873.pdf

Closed 2019-12-18.

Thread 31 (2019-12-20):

documentation of PCB hardware missing in documentation

JayWiz, 2019-12-20:
THere should be some documentation of the designed PCB in the readme of this repository!

JayWiz, 2020-01-30:
Duplicate of #10

Closed 2020-01-30.

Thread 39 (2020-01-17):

Animations and progress indication on LED Matrix

JayWiz, 2020-01-17:
Currently, you can just see Some circles and rectangles, and a "Solved" on the LED matrix.
This should be replaced with a better visualization, for example instructions, some fancy movements and so on

JayWiz, 2020-02-04:
Done

Closed 2020-02-04.

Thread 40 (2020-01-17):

No function in upper right corner

JayWiz, 2020-01-17:
The fusebox pcb has some buttons and LEDs in the upper right corner, which can be controlled via I2C. Right now, theres no function. Implement some logic, e.g. controlling the LED matrix with those buttons

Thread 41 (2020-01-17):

ADC2 not working with WiFi

JayWiz, 2020-01-17:
ADC2 cannot be used while using WiFI in a normal way while using Arduino Framework
see: https://github.com/espressif/arduino-esp32/issues/102

JayWiz, 2020-01-21:
Workaround ATM: Single corresponding bit got new limits to fake a right value at this pin

maxim0815, 2020-01-23:
solved by leaving out this port. Now 4 wires instead of 5.

Closed 2020-01-23.

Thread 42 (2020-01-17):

Laser detection and riddles parallel

JayWiz, 2020-01-17:
Would prevent crashing

Closed 2020-01-21.

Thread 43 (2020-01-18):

Parametrize Watchdog Timer

JayWiz, 2020-01-18:
Could be useful

JayWiz, 2020-01-21:
currently, Watchdogs are not disabled, but also not parametrized

JayWiz, 2020-01-30:
not needed, there are no crasher anymore

Closed 2020-01-30.

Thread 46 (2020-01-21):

Serial Print in Fusebox

JayWiz, 2020-01-21:
Replace Serial Print in Fusebox with a Function with some logic and defines

JayWiz, 2020-01-21:
Done

Closed 2020-01-21.

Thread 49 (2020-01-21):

New Mqtt State Handling

JayWiz, 2020-01-21:
Don't now whether there will be problems

JayWiz, 2020-01-23:
There is still some stuff to to:

- [ ] send status messages only on change, should reduce load on network

- [ ] status messages should always contain the retainedBits

- [ ] listen to trigger on, trigger of messages: server is just directly talking with clients via Trigger messages, also it should be possible to switch puzzles on/off

**TLDR:
status active and inactive are not that important, trigger on/off have to be implemented**

JayWiz, 2020-01-23:
**Idea how it could be implemented**

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

JayWiz, 2020-01-29:
done

Closed 2020-01-29.

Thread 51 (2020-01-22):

Check AWS FreeRTOS and Zepyhr RTOS

JayWiz, 2020-01-22:
Maybe they are better for the project

JayWiz, 2020-01-24:
AWS FreeRTOS just compatible with ESP-IDF, Zephyr currently not available for platformio, therefore both options are not feasible for fusebox

Closed 2020-01-24.

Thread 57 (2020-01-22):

Add Travis CI for button and robot

JayWiz, 2020-01-22:
Is already implemented for fusebox and laser, should still be done for other parts.
Just add enviroments variables for those subdirectories!

JayWiz, 2020-01-23:
Done, see #59

Closed 2020-01-23.

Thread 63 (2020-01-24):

fusebox, laser and robot com failed

TKoe92, 2020-01-24:
maybe after start of the game-logic of the operator the controllers crashed and did not receive any massage. The fusebox sent "null"

JayWiz, 2020-01-24:
Oof

JayWiz, 2020-01-29:
done

Closed 2020-01-29.

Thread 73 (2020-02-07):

Open FuseBox in case of skip riddle

maxim0815, 2020-02-07:

Closed 2020-02-08.

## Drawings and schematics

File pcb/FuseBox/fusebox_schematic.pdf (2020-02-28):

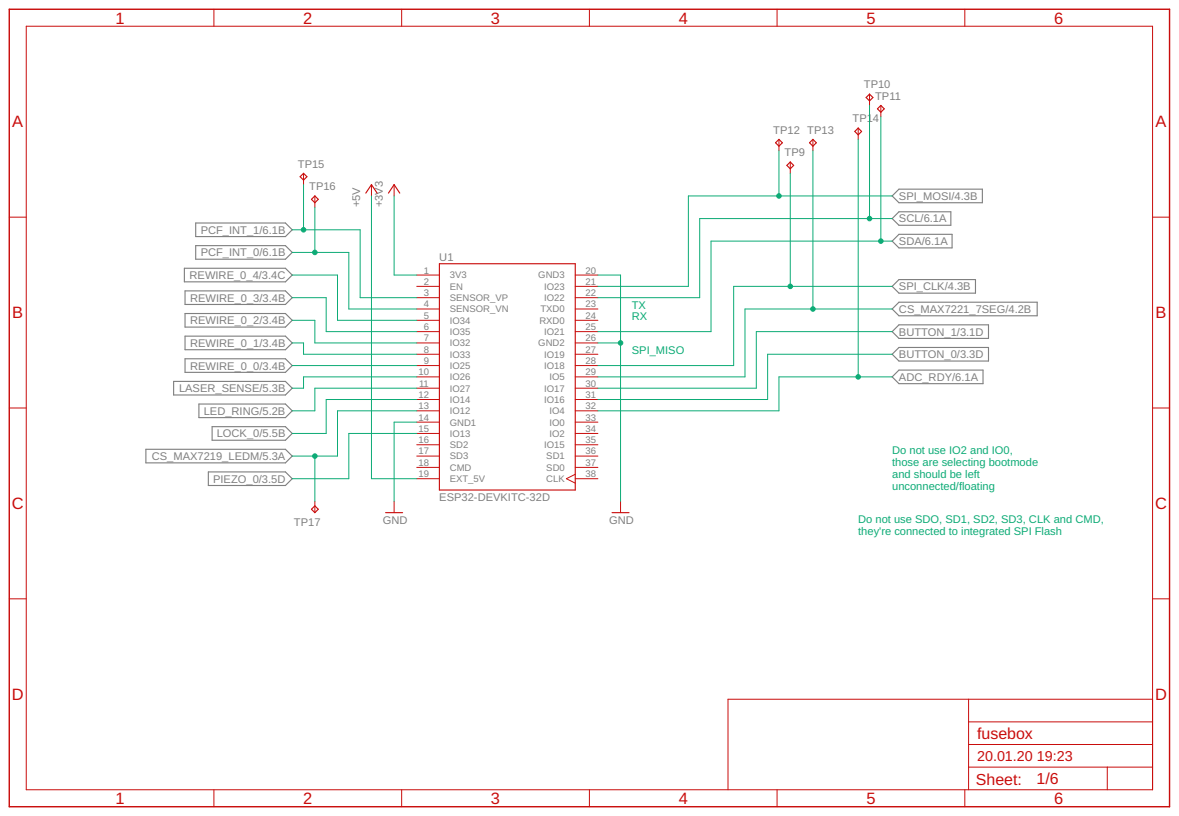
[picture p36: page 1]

7 | 26 | SPI_MISO
8 | 27 GND2 28

11 | 30
12 | 31

Do not use IO2 and IO0,
those are selecting bootmode
and should be left unconnected/floating

Do not use SDO, SD1, SD2, SD3, CLK and CMD,
they're connected to integrated SPI Flash

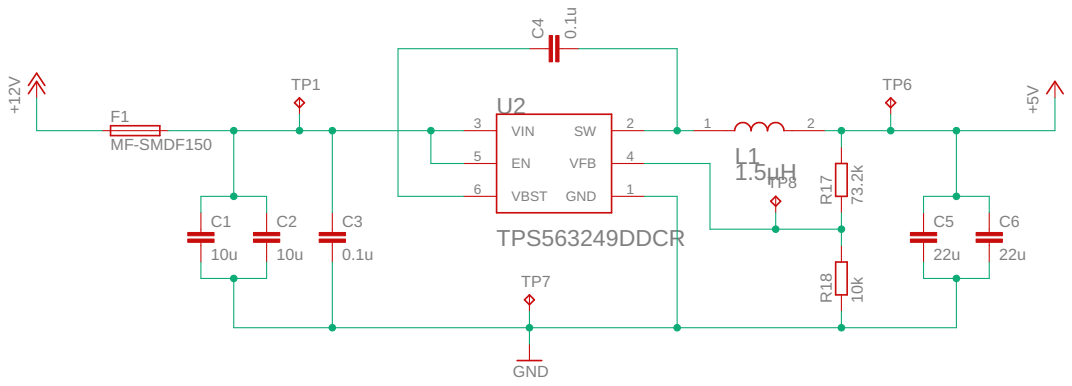
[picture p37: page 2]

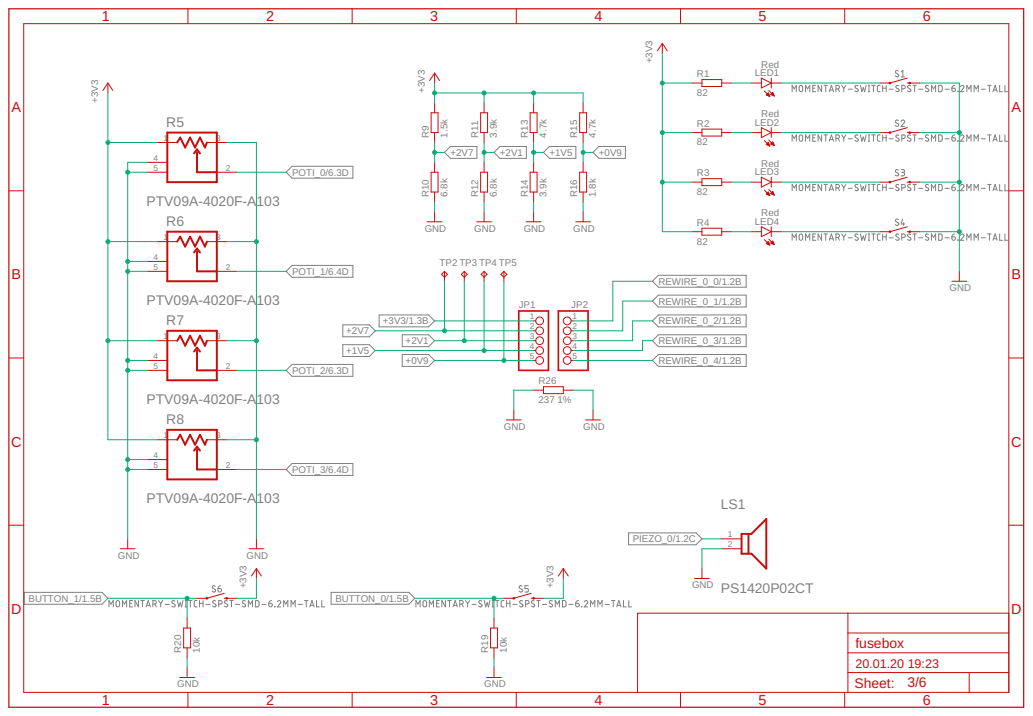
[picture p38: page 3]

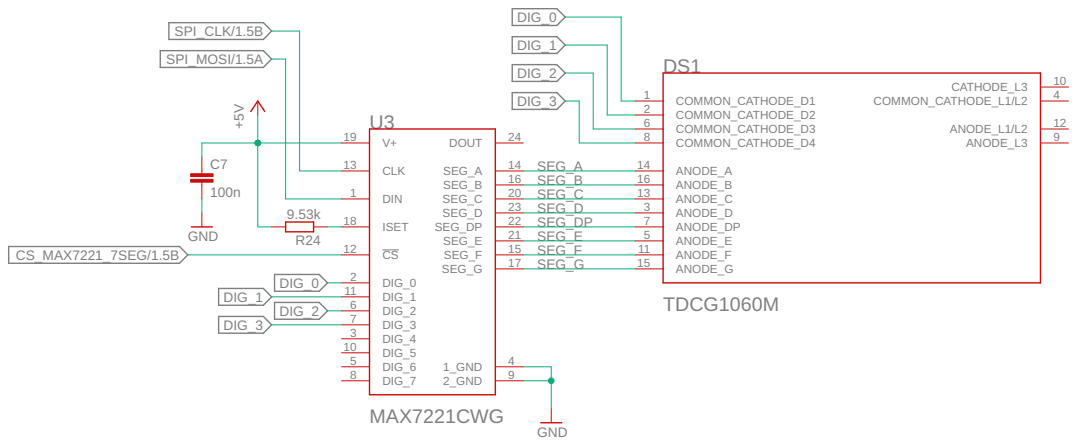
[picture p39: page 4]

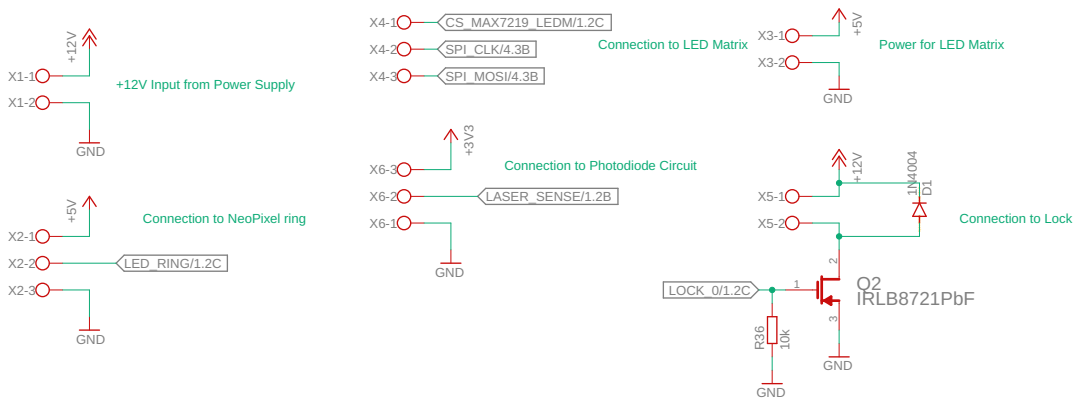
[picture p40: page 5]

+12V Input from Power Supply

GND

Connection to Photodiode Circuit

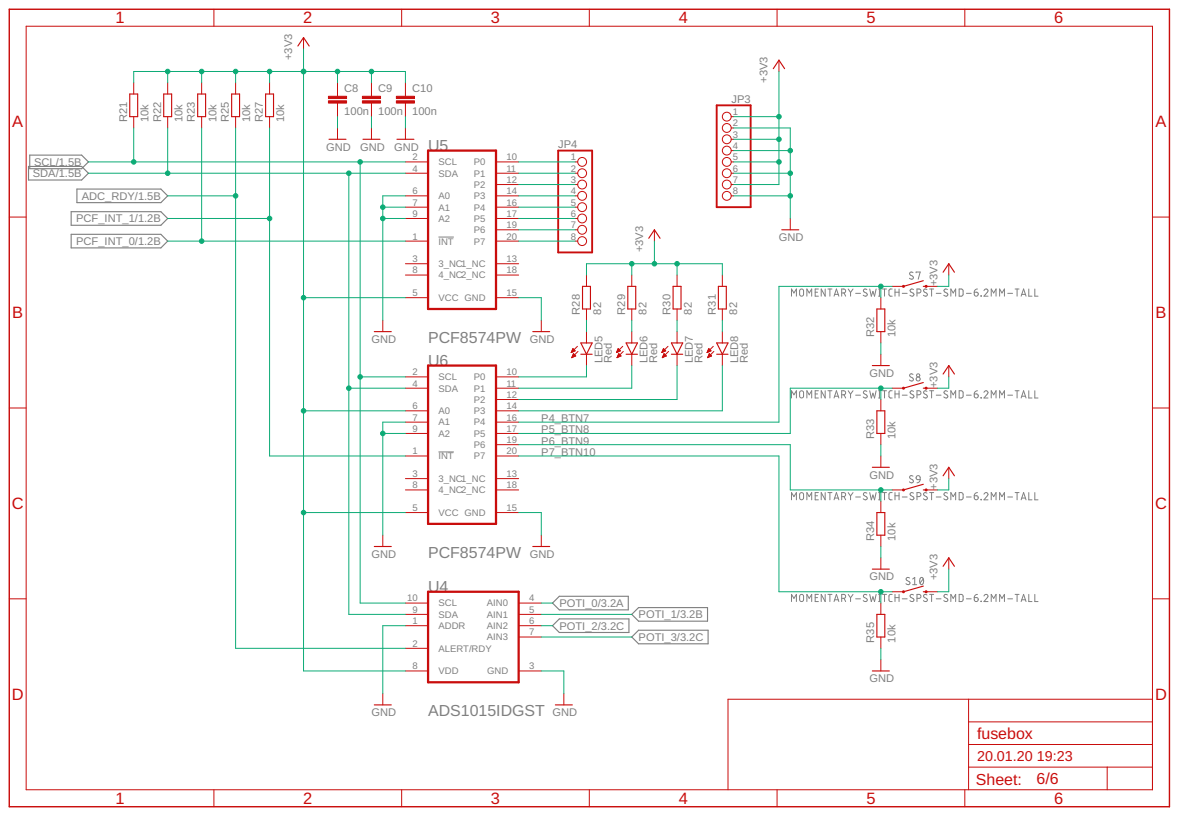
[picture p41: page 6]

+3V3 GND GND +3V3 10k 10k GND 10k100n GND 100n GND GND 10k GND GND GND 100n GND 10k Red 82 Red 82 Red 82 Red 82 +3V3 +3V3 10k GND +3V3 10k GND +3V3 10k GND +3V3 10k GND PCF8574PW INT 1 SCL 2 3_NC 3 SDA 4 VCC 5 A0 6 A1 7 4_NC 8 A2 9 P0 10 P1 11 P2 12 1_NC 13 P3 14 GND 15 P4 16 P5 17 2_NC 18 P6 19 P7 20 U5 12345678JP3 12345678 JP4 R21 R22 R23 C8 C9 ADS1015IDGST ADDR 1 ALERT/RDY 2 GND 3 AIN0 4 AIN1 5 AIN2 6 AIN3 7 VDD 8 SDA 9 SCL 10 U4 R25 PCF8574PW INT 1 SCL 2 3_NC 3 SDA 4 VCC 5 A0 6 A1 7 4_NC 8 A2 9 P0 10 P1 11 P2 12 1_NC 13 P3 14 GND 15 P4 16 P5 17 2_NC 18 P6 19 P7 20 U6 C10 R27 LED5 R28 LED6 R29 LED7 R30 LED8 R31 R32 R33 R34 R35 SCL/1.5B SDA/1.5BPCF_INT_0/1.2B ADC_RDY/1.5B POTI_0/3.2A POTI_1/3.2B POTI_2/3.2C POTI_3/3.2C PCF_INT_1/1.2B P4_BTN7 P5_BTN8 P6_BTN9 P7_BTN10 Sheet: ABCD 1 2 3 4 5 6 ABCD 1 2 3 4 5 6 fusebox 20.01.20 19:23 6/6

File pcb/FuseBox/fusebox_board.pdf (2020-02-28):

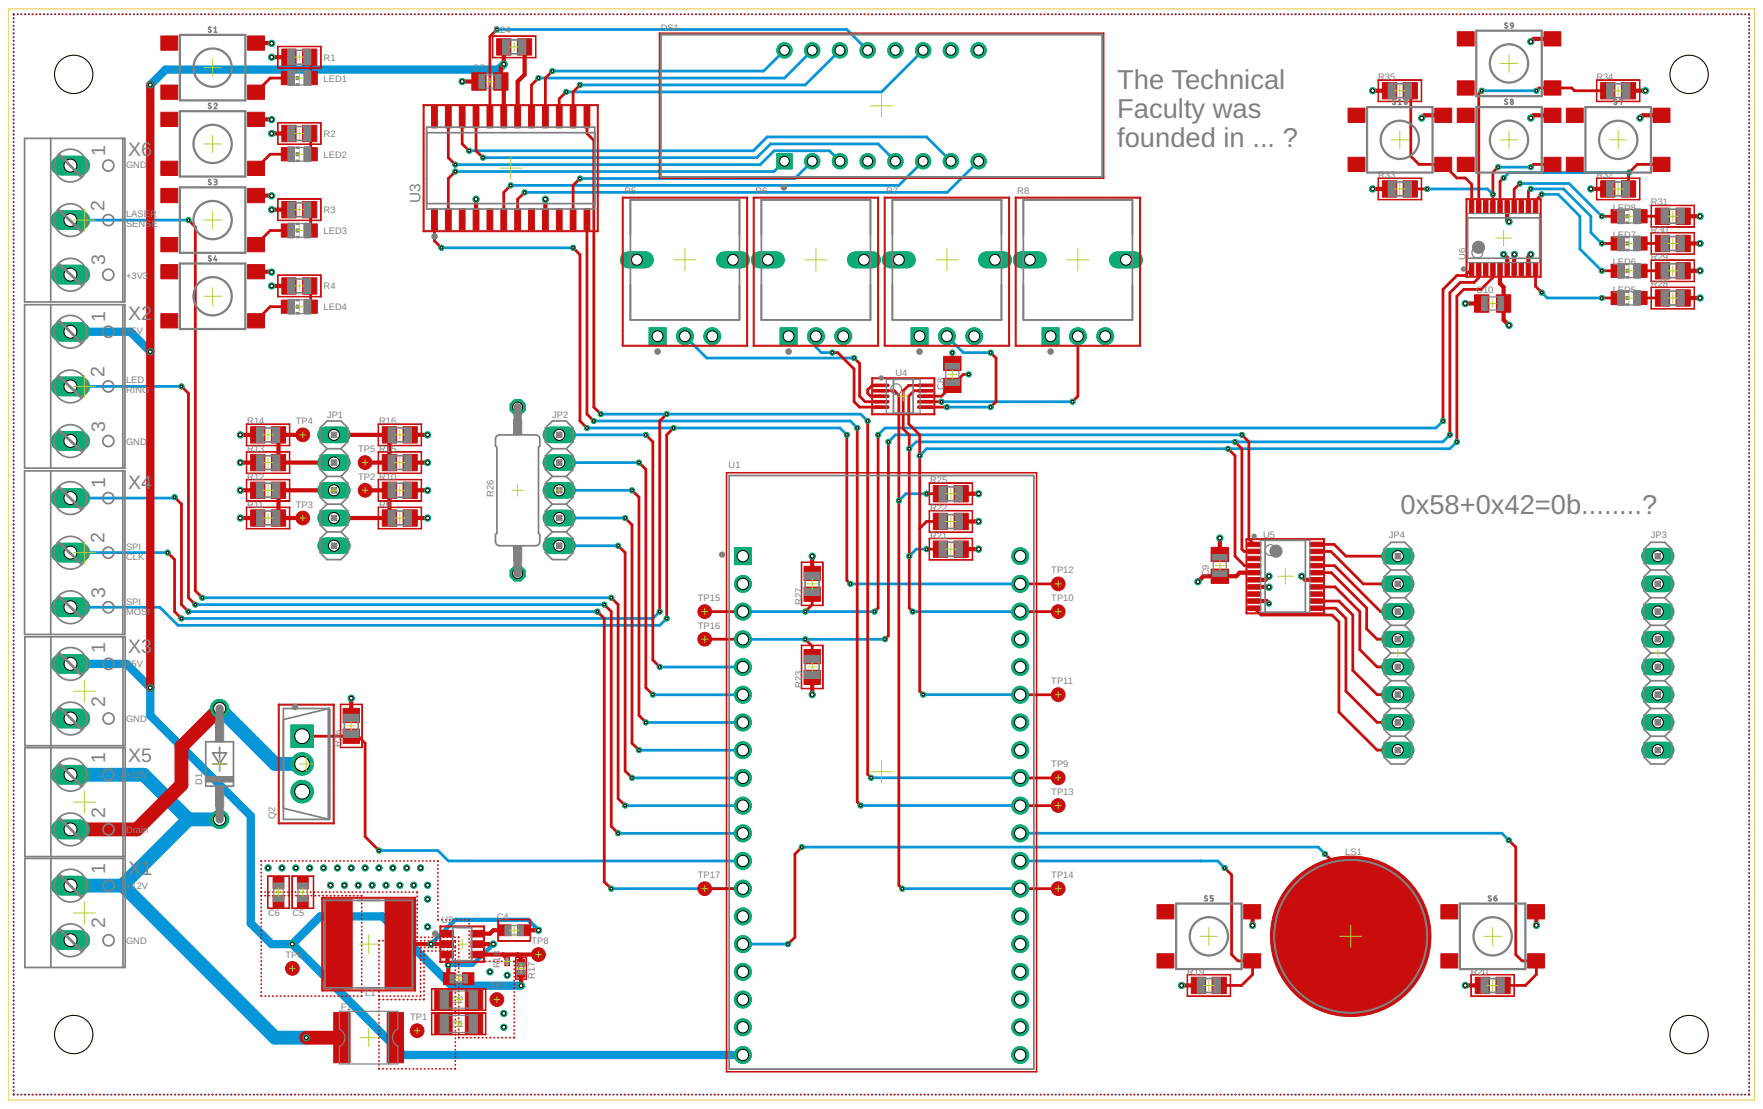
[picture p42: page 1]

1 2 1 2 1 2 1 2 3 1 2 3 1 2 3 0x58+0x42=0b........? The Technical Faculty was founded in ... ? GND GND GND GND LASER SENSE +3V3 +5V LED RING SPI CLK SPI MOSI +12V +12V Drain +5V U1 R5 R6 R7 R8 U3 DS1 LED1 LED2 LED3 LED4 R1 R2 R3 R4JP1 JP2 JP4 JP3 R9 R10 R11 R12 R13 R14 R15 R16 U2C1 C2C3 C4 L1 R1R718 C6 C5 X1X2 LS1 R19 R20 X3X4X5 D1 X6 R21 U5 R22 R23 R24 C7 C8 C9 U4 R25 TP1 R26 F1 TP2 TP3 TP4 TP5 U6 C10 R27 LED5 R28 LED6 R29 LED7 R30 LED8 R31 R33 R32 R35 R34 TP6 TP7 TP8 TP9 TP10 TP11 TP12 TP13 TP14 TP15 TP16 TP17 Q2 R36

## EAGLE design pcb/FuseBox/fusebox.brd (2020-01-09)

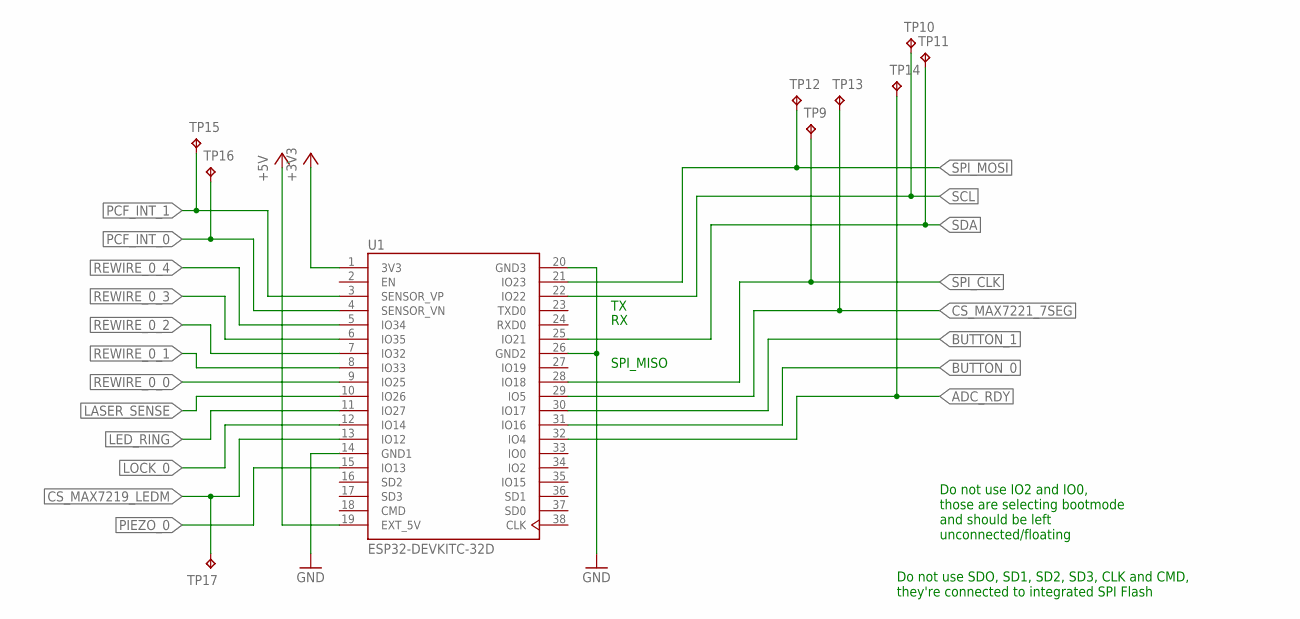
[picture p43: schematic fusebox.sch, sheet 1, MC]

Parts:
TP9, TP10, TP11, TP12, TP13, TP14, TP15, TP16, TP17: TPB1,27; B1,27
U1: ESP32-DEVKITC-32D; MODULE_ESP32-DEVKITC-32D

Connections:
+3V3: U1.1 (3V3); also elsewhere on the board
+5V: U1.19 (EXT_5V); also elsewhere on the board
ADC_RDY: TP14.TP, U1.32 (IO4); also elsewhere on the board
BUTTON_0: U1.31 (IO16); also elsewhere on the board
BUTTON_1: U1.30 (IO17); also elsewhere on the board
CS_MAX7219_LEDM: TP17.TP, U1.13 (IO12); also elsewhere on the board
CS_MAX7221_7SEG: TP13.TP, U1.29 (IO5); also elsewhere on the board
GND: U1.14 (GND1), U1.20 (GND3), U1.26 (GND2); also elsewhere on the board
LASER_SENSE: U1.10 (IO26); also elsewhere on the board
LED_RING: U1.11 (IO27); also elsewhere on the board
LOCK_0: U1.12 (IO14); also elsewhere on the board
PCF_INT_0: TP16.TP, U1.4 (SENSOR_VN); also elsewhere on the board
PCF_INT_1: TP15.TP, U1.3 (SENSOR_VP); also elsewhere on the board
PIEZO_0: U1.15 (IO13); also elsewhere on the board
REWIRE_0_0: U1.9 (IO25); also elsewhere on the board
REWIRE_0_1: U1.8 (IO33); also elsewhere on the board
REWIRE_0_2: U1.7 (IO32); also elsewhere on the board
REWIRE_0_3: U1.6 (IO35); also elsewhere on the board
REWIRE_0_4: U1.5 (IO34); also elsewhere on the board
SCL: TP10.TP, U1.22 (IO22); also elsewhere on the board
SDA: TP11.TP, U1.25 (IO21); also elsewhere on the board
SPI_CLK: TP9.TP, U1.28 (IO18); also elsewhere on the board
SPI_MOSI: TP12.TP, U1.21 (IO23); also elsewhere on the board

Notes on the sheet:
SPI_MISO
Do not use IO2 and IO0, those are selecting bootmode and should be left unconnected/floating
Do not use SDO, SD1, SD2, SD3, CLK and CMD, they're connected to integrated SPI Flash

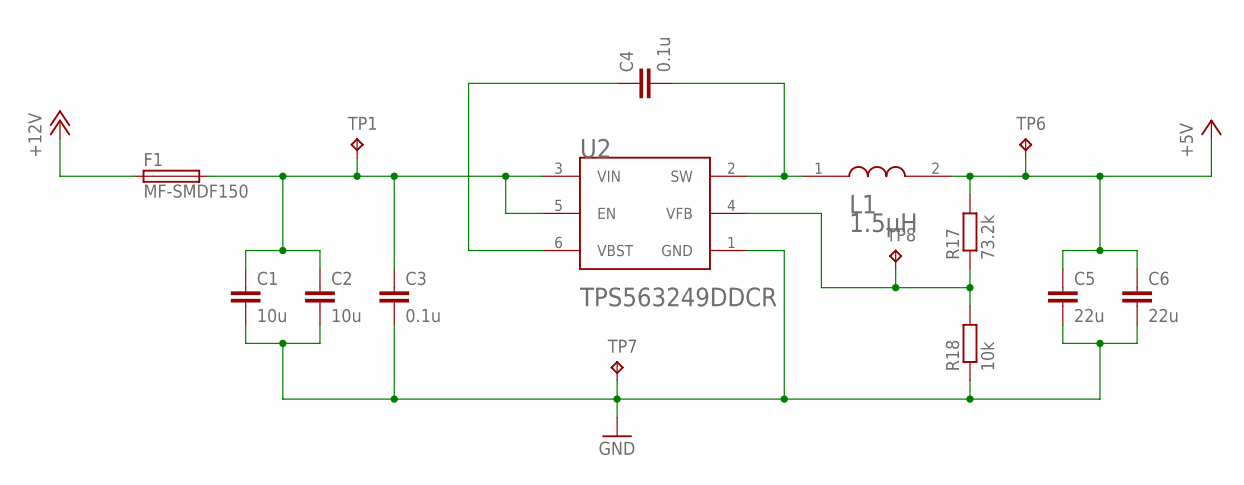
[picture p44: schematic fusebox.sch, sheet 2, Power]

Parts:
C1, C2: 10u; C1206
C3: 0.1u; C0603K
C4: 0.1u; C0603
C5, C6: 22u; C0603
F1: MF-SMDF150; MF-SMDF050
L1: BOURNS_SRN8040-1R5YBOURNS_SRN8040-1R5Y_0_0; BOURNS_SRN8040-1R5Y_0
R17: 73.2k; R0402
R18: 10k; R0201
TP1, TP6, TP7, TP8: TPB1,27; B1,27
U2: TEXAS_INSTRUMENTS_TPS563249DDCRTEXAS_INSTRUMENTS_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; TEXAS_INSTRUMENTS_TPS563249DDCR_0

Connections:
+5V: C5.1, C6.1, L1.2, R17.2, TP6.TP; also elsewhere on the board
+12V: F1.1; also elsewhere on the board
GND: C1.2, C2.2, C3.2, C5.2, C6.2, R18.1, TP7.TP, U2.1 (GND); also elsewhere on the board
unnamed: C1.1, C2.1, C3.1, F1.2, TP1.TP, U2.3 (VIN), U2.5 (EN)
unnamed: C4.1, U2.6 (VBST)
unnamed: C4.2, L1.1, U2.2 (SW)
unnamed: R17.1, R18.2, TP8.TP, U2.4 (VFB)

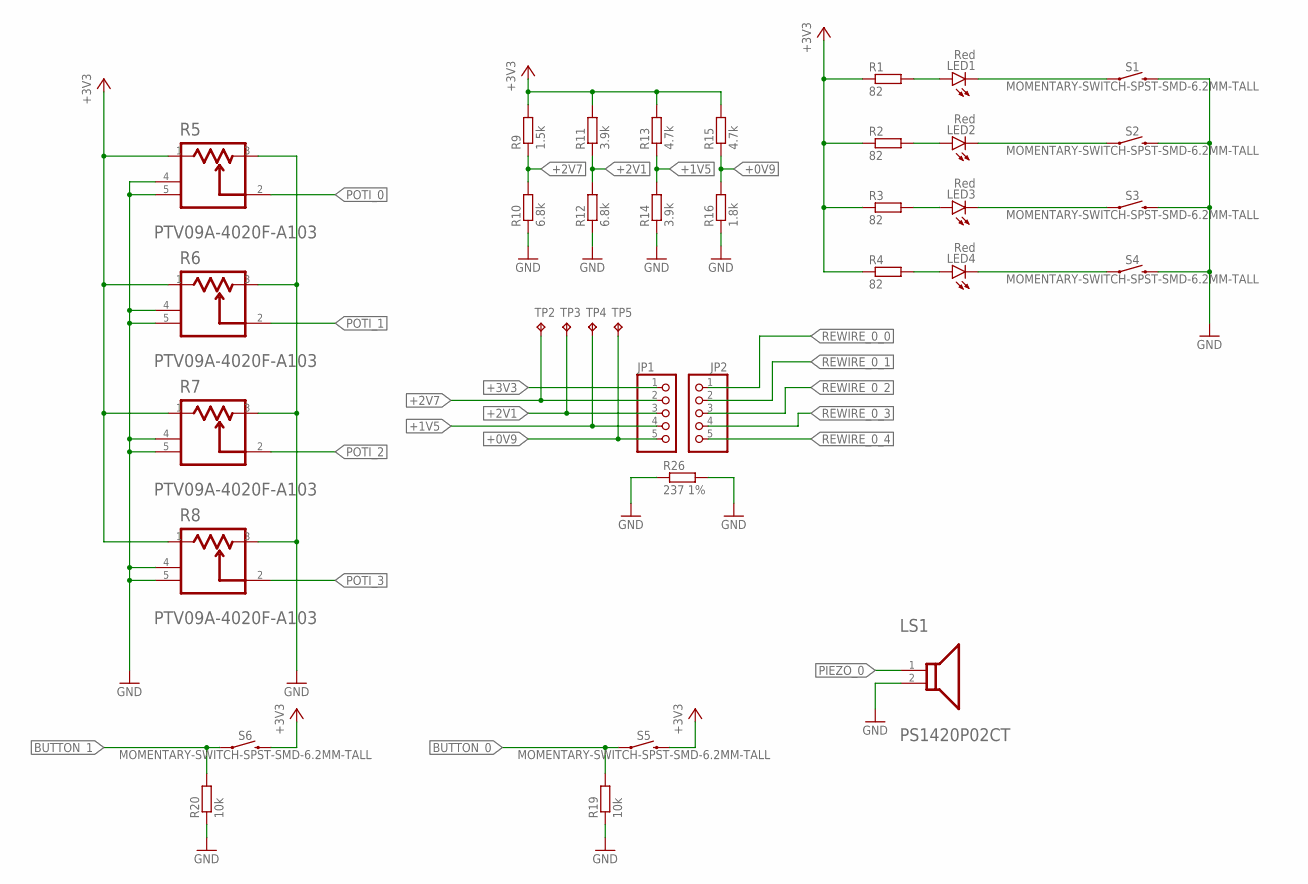
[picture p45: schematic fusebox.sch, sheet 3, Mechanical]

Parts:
JP1, JP2: PINHD-1X5; 1X05
LED1, LED2, LED3, LED4: Red; CHIP-LED0805
LS1: TDK_PS1420P02CTTDK_PS1420P02CT_0_0; TDK_PS1420P02CT_0
R1, R2, R3, R4: 82; R0805
R5, R6, R7, R8: BOURNS_PTV09A-4020F-A103BOURNS_PTV09A-4020F-A103_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; BOURNS_PTV09A-4020F-A103_0
R9: 1.5k; R0805
R10, R12: 6.8k; R0805
R11, R14: 3.9k; R0805
R13, R15: 4.7k; R0805
R16: 1.8k; R0805
R19, R20: 10k; R0805
R26: 237 1%; 0411/15
S1, S2, S3, S4, S5, S6: MOMENTARY-SWITCH-SPST-SMD-6.2MM-TALL; TACTILE_SWITCH_SMD_6.2MM_TALL
TP2, TP3, TP4, TP5: TPB1,27; B1,27

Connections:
+0V9: JP1.5, R15.1, R16.2, TP5.TP
+1V5: JP1.4, R13.1, R14.2, TP4.TP
+2V1: JP1.3, R11.1, R12.2, TP3.TP
+2V7: JP1.2, R9.1, R10.2, TP2.TP
+3V3: JP1.1, R1.1, R2.1, R3.1, R4.1, R5.1, R6.1, R7.1, R8.1, R9.2, R11.2, R13.2, R15.2, S5.B2 (2), S6.B2 (2); also elsewhere on the board
BUTTON_0: R19.2, S5.A2 (1); also elsewhere on the board
BUTTON_1: R20.2, S6.A2 (1); also elsewhere on the board
GND: LS1.2, R5.3, R5.4 (MNT_1), R5.5 (MNT_2), R6.3, R6.4 (MNT_1), R6.5 (MNT_2), R7.3, R7.4 (MNT_1), R7.5 (MNT_2), R8.3, R8.4 (MNT_1), R8.5 (MNT_2), R10.1, R12.1, R14.1, R16.1, R19.1, R20.1, R26.1, R26.2, S1.B2 (2), S2.B2 (2), S3.B2 (2), S4.B2 (2); also elsewhere on the board
unnamed: LED1.A, R1.2
unnamed: LED2.A, R2.2
unnamed: LED3.A, R3.2
unnamed: LED4.A, R4.2
unnamed: LED1.C, S1.A2 (1)
unnamed: LED2.C, S2.A2 (1)
unnamed: LED3.C, S3.A2 (1)
unnamed: LED4.C, S4.A2 (1)
PIEZO_0: LS1.1; also elsewhere on the board
POTI_0: R5.2; also elsewhere on the board
POTI_1: R6.2; also elsewhere on the board
POTI_2: R7.2; also elsewhere on the board
POTI_3: R8.2; also elsewhere on the board
REWIRE_0_0: JP2.1; also elsewhere on the board
REWIRE_0_1: JP2.2; also elsewhere on the board
REWIRE_0_2: JP2.3; also elsewhere on the board
REWIRE_0_3: JP2.4; also elsewhere on the board
REWIRE_0_4: JP2.5; also elsewhere on the board

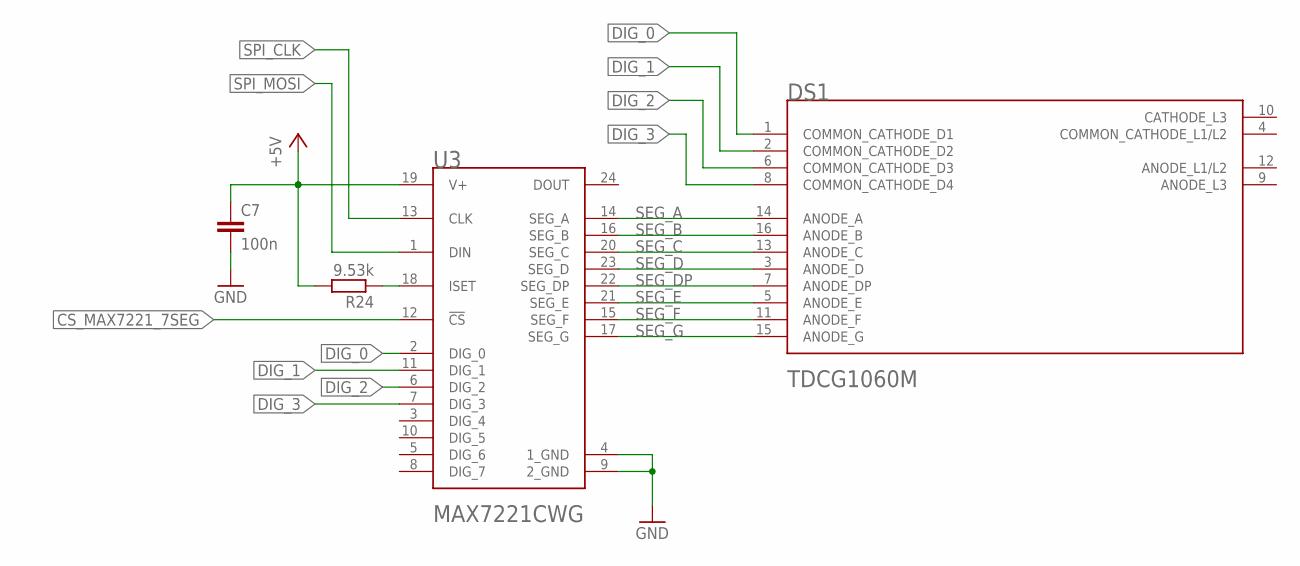
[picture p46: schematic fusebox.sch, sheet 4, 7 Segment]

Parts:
C7: 100n; C0805K
DS1: VISHAY_TDCG1060MVISHAY_TDCG1060M_0_0; VISHAY_TDCG1060M_0
R24: 9.53k; R0805
U3: MAXIM_ELECTRONICS_MAX7221CWGMAXIM_ELECTRONICS_MAX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; MAXIM_ELECTRONICS_MAX7221CWG_0

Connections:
+5V: C7.1, R24.2, U3.19 (V+); also elsewhere on the board
CS_MAX7221_7SEG: U3.12 (!CS!); also elsewhere on the board
DIG_0: DS1.1 (COMMON_CATHODE_D1), U3.2 (DIG_0)
DIG_1: DS1.2 (COMMON_CATHODE_D2), U3.11 (DIG_1)
DIG_2: DS1.6 (COMMON_CATHODE_D3), U3.6 (DIG_2)
DIG_3: DS1.8 (COMMON_CATHODE_D4), U3.7 (DIG_3)
GND: C7.2, U3.4 (1_GND), U3.9 (2_GND); also elsewhere on the board
unnamed: R24.1, U3.18 (ISET)
SEG_A: DS1.14 (ANODE_A), U3.14 (SEG_A)
SEG_B: DS1.16 (ANODE_B), U3.16 (SEG_B)
SEG_C: DS1.13 (ANODE_C), U3.20 (SEG_C)
SEG_D: DS1.3 (ANODE_D), U3.23 (SEG_D)
SEG_DP: DS1.7 (ANODE_DP), U3.22 (SEG_DP)
SEG_E: DS1.5 (ANODE_E), U3.21 (SEG_E)
SEG_F: DS1.11 (ANODE_F), U3.15 (SEG_F)
SEG_G: DS1.15 (ANODE_G), U3.17 (SEG_G)
SPI_CLK: U3.13 (CLK); also elsewhere on the board
SPI_MOSI: U3.1 (DIN); also elsewhere on the board

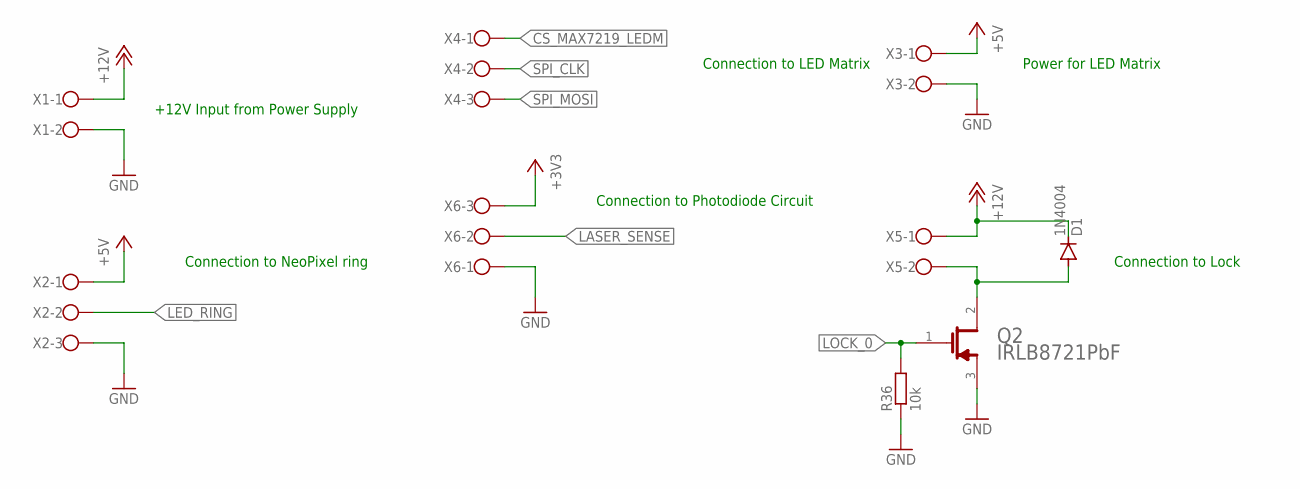
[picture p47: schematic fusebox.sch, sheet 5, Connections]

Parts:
D1: 1N4004; DO41-10
Q2: INFINEON_IRLB8721PBFINFINEON_IRLB8721PBF_0_0; INFINEON_IRLB8721PBF_0
R36: 10k; R0805
X1, X3, X5: W237-102
X2, X4, X6: W237-103

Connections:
+3V3: X6.3; also elsewhere on the board
+5V: X2.1, X3.1; also elsewhere on the board
+12V: D1.C, X1.1, X5.1; also elsewhere on the board
CS_MAX7219_LEDM: X4.1; also elsewhere on the board
GND: Q2.3 (S), R36.1, X1.2, X2.3, X3.2, X6.1; also elsewhere on the board
LASER_SENSE: X6.2; also elsewhere on the board
LED_RING: X2.2; also elsewhere on the board
LOCK_0: Q2.1 (G), R36.2; also elsewhere on the board
unnamed: D1.A, Q2.2 (D), X5.2
SPI_CLK: X4.2; also elsewhere on the board
SPI_MOSI: X4.3; also elsewhere on the board

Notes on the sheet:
+12V Input from Power Supply
Connection to LED Matrix
Power for LED Matrix
Connection to Photodiode Circuit
Connection to Lock
Connection to NeoPixel ring

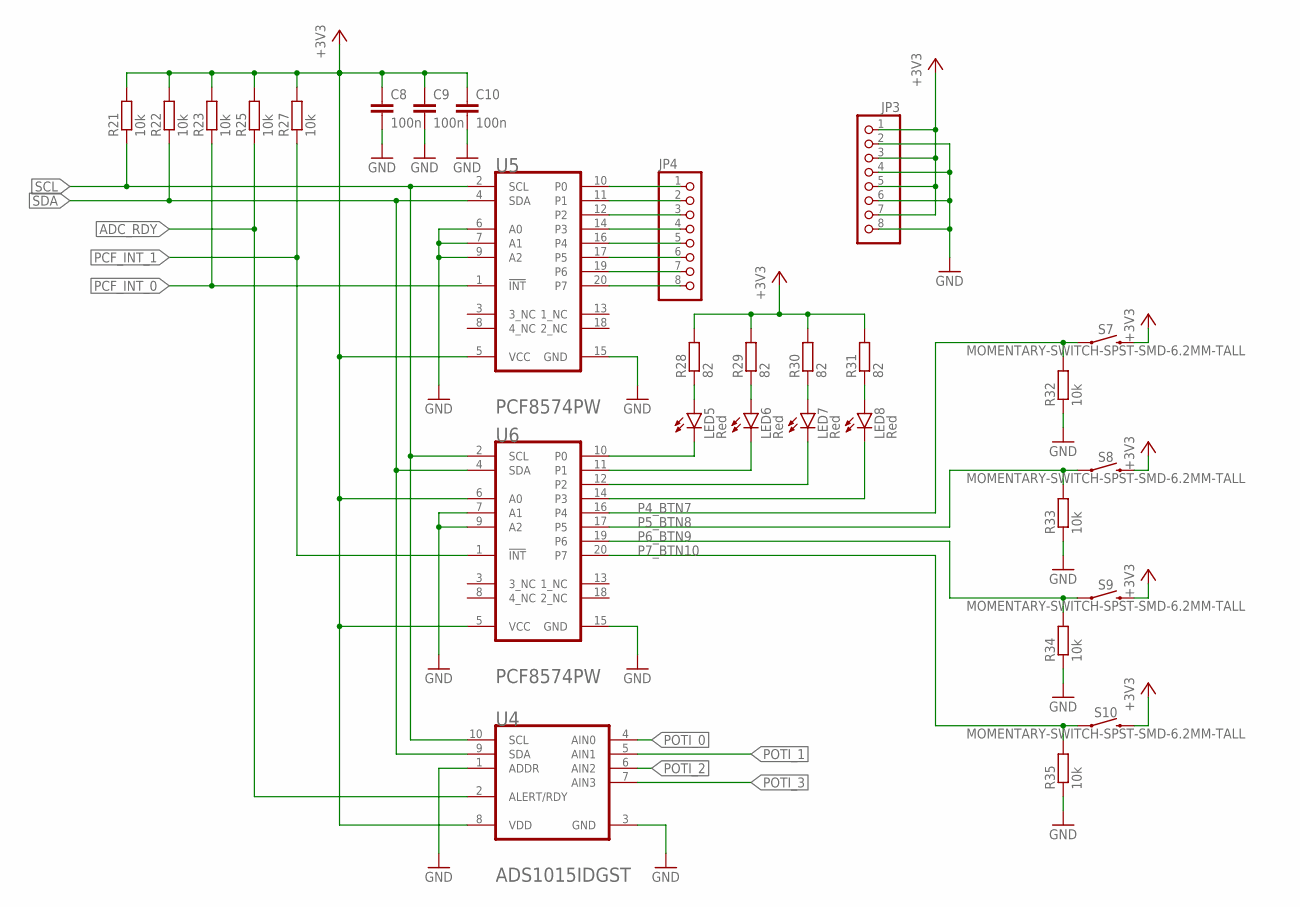
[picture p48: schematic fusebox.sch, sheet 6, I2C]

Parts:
C8, C9, C10: 100n; C0805K
JP3, JP4: PINHD-1X8; 1X08
LED5, LED6, LED7, LED8: Red; CHIP-LED0805
R21, R22, R23, R25, R27, R32, R33, R34, R35: 10k; R0805
R28, R29, R30, R31: 82; R0805
S7, S8, S9, S10: MOMENTARY-SWITCH-SPST-SMD-6.2MM-TALL; TACTILE_SWITCH_SMD_6.2MM_TALL
U4: TEXAS_INSTRUMENTS_ADS1015IDGSTTEXAS_INSTRUMENTS_A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; TEXAS_INSTRUMENTS_ADS1015IDGST_0
U5, U6: TEXAS_INSTRUMENTS_PCF8574PWTEXAS_INSTRUMENTS_PCF8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; TEXAS_INSTRUMENTS_PCF8574PW_0

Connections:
+3V3: C8.1, C9.1, C10.1, JP3.1, JP3.3, JP3.5, JP3.7, R21.2, R22.2, R23.2, R25.2, R27.2, R28.2, R29.2, R30.2, R31.2, S7.B2 (2), S8.B2 (2), S9.B2 (2), S10.B2 (2), U4.8 (VDD), U5.5 (VCC), U6.5 (VCC), U6.6 (A0); also elsewhere on the board
ADC_RDY: R25.1, U4.2 (ALERT/RDY); also elsewhere on the board
GND: C8.2, C9.2, C10.2, JP3.2, JP3.4, JP3.6, JP3.8, R32.1, R33.1, R34.1, R35.1, U4.1 (ADDR), U4.3 (GND), U5.6 (A0), U5.7 (A1), U5.9 (A2), U5.15 (GND), U6.7 (A1), U6.9 (A2), U6.15 (GND); also elsewhere on the board
unnamed: LED5.A, R28.1
unnamed: LED5.C, U6.10 (P0)
unnamed: LED6.A, R29.1
unnamed: LED6.C, U6.11 (P1)
unnamed: LED7.A, R30.1
unnamed: LED7.C, U6.12 (P2)
unnamed: JP4.1, U5.10 (P0)
unnamed: JP4.2, U5.11 (P1)
unnamed: JP4.3, U5.12 (P2)
unnamed: JP4.4, U5.14 (P3)
unnamed: JP4.5, U5.16 (P4)
unnamed: JP4.6, U5.17 (P5)
unnamed: JP4.7, U5.19 (P6)
unnamed: JP4.8, U5.20 (P7)
unnamed: LED8.A, R31.1
unnamed: LED8.C, U6.14 (P3)
P4_BTN7: R32.2, S7.A2 (1), U6.16 (P4)
P5_BTN8: R33.2, S8.A2 (1), U6.17 (P5)
P6_BTN9: R34.2, S9.A2 (1), U6.19 (P6)
P7_BTN10: R35.2, S10.A2 (1), U6.20 (P7)
PCF_INT_0: R23.1, U5.1 (!INT!); also elsewhere on the board
PCF_INT_1: R27.1, U6.1 (!INT!); also elsewhere on the board
POTI_0: U4.4 (AIN0); also elsewhere on the board
POTI_1: U4.5 (AIN1); also elsewhere on the board
POTI_2: U4.6 (AIN2); also elsewhere on the board
POTI_3: U4.7 (AIN3); also elsewhere on the board
SCL: R21.1, U4.10 (SCL), U5.2 (SCL), U6.2 (SCL); also elsewhere on the board
SDA: R22.1, U4.9 (SDA), U5.4 (SDA), U6.4 (SDA); also elsewhere on the board

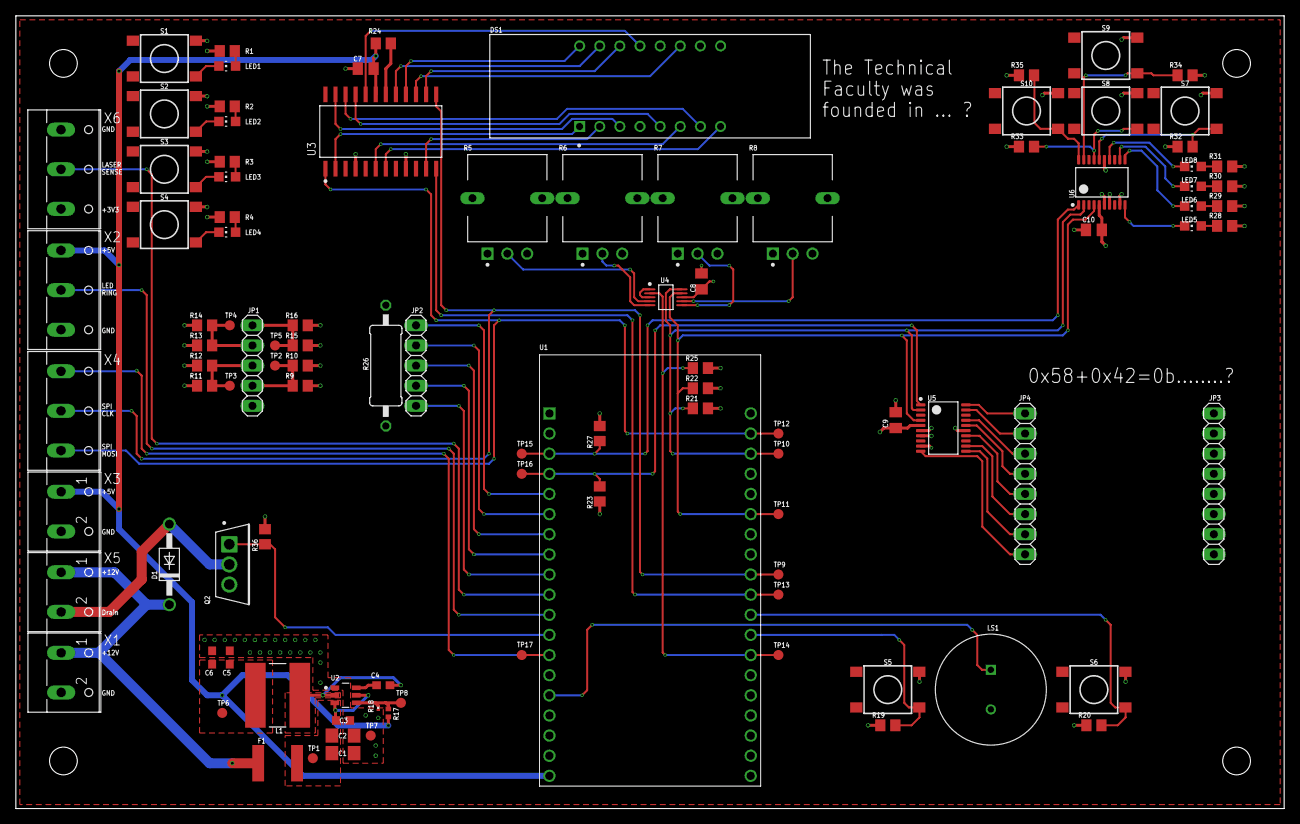
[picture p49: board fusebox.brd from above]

Board: 2 copper layers, 160.0 x 100.0 mm, 103 parts (0 on the bottom side), 78 nets.

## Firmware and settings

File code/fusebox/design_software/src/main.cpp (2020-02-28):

// define this to get serial debug messages
#define SERIAL_DEBUG

// Import All Libraries
#include "Fonts.h"
// This is a library i wrote to handle MAX7221 7 Segment
#include "MAX7221.h"
#include "Wire.h"
// header File for serial debug commands
#include <Adafruit_ADS1015.h>
#include <Arduino.h>
#include <MD_MAX72xx.h>
#include <MD_MAXPanel.h>
#include <NeoPixelBus.h>
#include "serial_debug.h"
#include "wifi_secure.h"
// MqttBase is a library we wrote to handle MQTT Communication
// see https://github.com/JayWiz/MqttBase
#include <MqttBase.h>
#include <pcf8574_esp.h>
#include <vector>

// parameters for led ring
#define colorSaturation 128
RgbColor red(colorSaturation, 0, 0);
RgbColor green(0, colorSaturation, 0);
RgbColor blue(0, 0, colorSaturation);
RgbColor white(colorSaturation);
RgbColor black(0);

#if CONFIG_FREERTOS_UNICORE
#define ARDUINO_RUNNING_CORE 0
#else
#define ARDUINO_RUNNING_CORE 1
#endif

// delay times for task scheduler
#define INIT_DELAY 1000
#define INACTIVE_DELAY 5000
#define SOLVED_DELAY 1000

// chip select for led matrix and 7 segment
#define MAX7221_CS 5
#define MAX7219_CS 12

// everything else, mostly pin connections
#define PIEZO_0 13
#define BUTTON_0 16
#define BUTTON_1 17
#define LEDC_CHANNEL1 0
#define LEDC_RESOLUTION 8
#define LOCK_0 14
#define SEQUENDE_SIZE 5
#define MAX_SEQUENZES 32
#define RGB_RING_PIN 27
#define NUM_PIXEL 16
#define detectorPin 26
#define REWIRE_0_1 25
#define REWIRE_0_2 33
#define REWIRE_0_3 32
#define REWIRE_0_4 35
#define REWIRE_0_5 34

// Puzzle States
enum tPuzzleState { INACTIVE, ACTIVE, SOLVED, UNSOLVED, INIT };

tPuzzleState statePotentiometer;
tPuzzleState stateRewiring0;
tPuzzleState stateRewiring1;
tPuzzleState stateLaserDetection;

// bool for initial ledRing colors
bool laserDetectionInitialActivation = false;

// 7 Segment
MAX7221 seg1 = MAX7221(MAX7221_CS, 1, MAX7221::SEGMENT);

// LedMatrix
MD_MAXPanel ledm1 = MD_MAXPanel(MD_MAX72XX::FC16_HW, MAX7219_CS, 4, 2);

// Led Ring
NeoPixelBus<NeoGrbFeature, Neo800KbpsMethod> pixels(NUM_PIXEL, RGB_RING_PIN);
uint8_t sequence[6];
uint8_t numberOfSequences = 0;
int old_time_in_ms = millis();
bool puzzle_solved = false;
void blink_ring(uint8_t blinking_number, uint8_t frequency);
uint8_t analyse_sequence(uint8_t sequence[6], uint8_t target);

// ADC
Adafruit_ADS1015 ads;

// Port Expander
PCF857x portExpander0(0x20, &Wire);
PCF857x portExpander1(0x21, &Wire);

// MQTT callback definitions
MqttBase *mqttCommunication;
void callbackLaserDetection(const char *method1, const char *state, int daten);
void callbackRewiring0(const char *method1, const char *state, int daten);
void callbackRewiring1(const char *method1, const char *state, int daten);
void callbackPotentiometer(const char *method1, const char *state, int daten);

// Task Definitions
void TaskPotentiometer(void *pvParameters);
void TaskWiring0Readout(void *pvParameters);
void TaskWiring1Readout(void *pvParameters);
void TaskPiezoButtonReadout(void *pvParameters);
void TaskControlPuzzleState(void *pvParameters);
void TaskLaserLock(void *pvParameters);
void TaskControlButtonsReadout(void *pvParameters);  // TODO: Implement
void TaskMqttLoop(void *pvParameters);
void TaskMqttPublish(void *pvParameters);

// Task Handles
TaskHandle_t xHandleLedRing;
TaskHandle_t xHandleControlPuzzleState;
TaskHandle_t xHandlePotentiometer;
TaskHandle_t xHandleWiring0Readout;
TaskHandle_t xHandleWiring1Readout;
TaskHandle_t xHandleMqttLoop;
TaskHandle_t xHandleMqttPublish;

// Delays
TickType_t xDelay1000ms = pdMS_TO_TICKS(1000);
TickType_t xDelay2000ms = pdMS_TO_TICKS(2000);

// Init Function Definitions
void initPotentiometer(void);
void initLaserDetection(void);
void initRewiring(void);

void initPiezoBuzzer(void);
void initLedMatrix(void);
void initMqtt(void);

void setup() {
  Serial.begin(115200);
  Serial.println("Setup started ...");

  // not needed
  // disableCore0WDT();
  // disableCore1WDT();

  // Start with init of all subcomponents
  initMqtt();
  vTaskDelay(1000);

  initPotentiometer();
  initLaserDetection();
  initRewiring();

  initPiezoBuzzer();
  initLedMatrix();

  Serial.println("Setup finished");

  // Attach Control Task
  xTaskCreatePinnedToCore(TaskControlPuzzleState, "TaskControlPuzzleState",
                          8192, NULL, 3, &xHandleControlPuzzleState, 1);

  // Mqtt Task
  xTaskCreatePinnedToCore(TaskMqttLoop, "TaskMqttLoop", 8192, NULL, 1,
                          &xHandleMqttLoop, 0);

  // Piezo Button Task
  xTaskCreatePinnedToCore(TaskPiezoButtonReadout, "TaskPiezoButtonReadout",
                          4096, NULL, 5, NULL, 1);

  // Puzzles Task Attachments (stack size, no parameters, task priority,
  // taskhandle and running Core)
  xTaskCreatePinnedToCore(TaskPotentiometer, "TaskPotentiometer", 8192, NULL, 3,
                          &xHandlePotentiometer, 1);
  xTaskCreatePinnedToCore(TaskLaserLock, "TaskLaserLock", 8192, NULL, 3,
                          &xHandleLedRing, 1);
  xTaskCreatePinnedToCore(TaskWiring0Readout, "TaskWiring0Readout", 8192, NULL,
                          3, &xHandleWiring0Readout, 1);
  xTaskCreatePinnedToCore(TaskWiring1Readout, "TaskWiring1Readout", 8192, NULL,
                          3, &xHandleWiring1Readout, 1);
}

void loop() {
  // no code here!
  // delete normal "arduino task"
  vTaskDelete(NULL);
}

void initLedMatrix(void) {
  Serial.print("Setup LED Matrix ... ");
  ledm1.begin();
  // set smaller font
  ledm1.setFont(_Fixed_5x3);
  Serial.println("done!");
}

void initPotentiometer(void) {
  Serial.print("Setup Potentiometer ... ");
  // init MAX and ADC
  seg1.initMAX();
  ads.begin();
  statePotentiometer = INIT;
  Serial.println("done!");
}

void initPiezoBuzzer(void) {
  Serial.print("Setup Piezobuzzer ... ");
  pinMode(BUTTON_0, INPUT);
  pinMode(BUTTON_1, INPUT);
  // Init PWM Signals for Buzzers
  ledcSetup(LEDC_CHANNEL1, 2000, LEDC_RESOLUTION);
  ledcAttachPin(PIEZO_0, LEDC_CHANNEL1);
  Serial.println("done!");
}

void initRewiring(void) {
  Serial.print("Setup Port Expander ... ");
  // Init I2C port expanders for rewiring readouts
  portExpander0.begin();
  portExpander1.begin();
  stateRewiring0 = INIT;
  stateRewiring1 = INIT;
  Serial.println("done!");
}

void initLaserDetection(void) {
  Serial.print("Setup LED Ring ... ");
  pixels.Begin();
  pixels.Show();  // Alle NeoPixel sind im status "aus".

  // no color in init
  for (int i = 0; i < NUM_PIXEL; i++) {
    pixels.SetPixelColor(i, black);
    pixels.Show();
  }
  pinMode(detectorPin, INPUT);  // Laser Detector als Eingangssignal setzen
  pinMode(LOCK_0, OUTPUT);      // Lock als Ausgang setzen

  stateLaserDetection = INIT;
  Serial.println("done!");
}

void initMqtt(void) {
  Serial.print("Setup MQTT ... ");

  // Create New MqttCommunication Object with IP adress, client name and port
  mqttCommunication = new MqttBase("10.0.0.2", "test187", 1883);

  // Create vector of shared_pointers of strings and add topic names
  std::vector<std::shared_ptr<std::string>> mqttTopics;
  mqttTopics.push_back(
      std::make_shared<std::string>("7/fusebox/laserDetection"));
  mqttTopics.push_back(std::make_shared<std::string>("7/fusebox/rewiring0"));
  mqttTopics.push_back(std::make_shared<std::string>("7/fusebox/rewiring1"));
  mqttTopics.push_back(
      std::make_shared<std::string>("7/fusebox/potentiometer"));

  // Create vectors of function pointers pointing to mqtt Callbacks
  std::vector<std::function<void(const char *, const char *, int)>>
      logicCallbacks;
  logicCallbacks.push_back(callbackLaserDetection);
  logicCallbacks.push_back(callbackRewiring0);
  logicCallbacks.push_back(callbackRewiring1);
  logicCallbacks.push_back(callbackPotentiometer);

  // call init function of mqttCommunication object with ssid, password & vector
  // of topicNames and logicCallbacks
  mqttCommunication->init(ssid, password, mqttTopics, logicCallbacks);

  Serial.println("done!");
}

void TaskPotentiometer(void *pvParameters) {
  (void)pvParameters;
  for (;;) {
    if (statePotentiometer == ACTIVE) {
      SERIALPRINTS("ACTIVE:\tTaskPotentiometer: \t")
      uint16_t pValues[4];
      float adcValues[4];
      for (uint8_t i = 0; i < 4; i++) {
        // read adc value, convert it and store it in array
        adcValues[i] = ads.readADC_SingleEnded(i);
        adcValues[i] = adcValues[i] * 9 / 1024;
        pValues[i] = adcValues[i];
        SERIALPRINT("", i);
        SERIALPRINTS(": ");
        SERIALPRINT("", pValues[i]);
        SERIALPRINTS(" ");
      }
      // suspend and resume after print (semaphore preventing race conditions on
      // spi bus)
      vTaskSuspend(xHandleControlPuzzleState);
      // print converted values on 7 segment
      seg1.transferData(0x01, pValues[0]);
      seg1.transferData(0x02, pValues[1]);
      seg1.transferData(0x03, pValues[2]);
      seg1.transferData(0x04, pValues[3]);
      vTaskResume(xHandleControlPuzzleState);
      // Check for 1995
      if (pValues[0] == 1 && pValues[1] == 9 && pValues[2] == 9 &&
          pValues[3] == 5) {
        SERIALPRINTS("Potis Solved!\n");
        statePotentiometer = SOLVED;
        // Publish to MQTT
        mqttCommunication->publish("7/fusebox/potentiometer", "status",
                                   "solved", true);
      } else {
        SERIALPRINTS("Potis not solved!\n");
        // statePotentiometer = UNSOLVED;
      }
      vTaskDelay(500);
    } else if (statePotentiometer == SOLVED) {
      SERIALPRINTS("SOLVED:\t\tTaskPotentiometer\n")
      // Show Solution
      seg1.transferData(0x01, 1);
      seg1.transferData(0x02, 9);
      seg1.transferData(0x03, 9);
      seg1.transferData(0x04, 5);
      vTaskDelay(SOLVED_DELAY);
    } else if (statePotentiometer == INACTIVE) {
      SERIALPRINTS("INACTIVE:\tTaskPotentiometer\n")
      // Show Solution
      seg1.transferData(0x01, 1);
      seg1.transferData(0x02, 9);
      seg1.transferData(0x03, 9);
      seg1.transferData(0x04, 5);
      vTaskDelay(INACTIVE_DELAY);
    } else if (statePotentiometer == INIT) {
      SERIALPRINTS("INIT:\t\tTaskPotentiometer\n")
      // Dont show Solution
      seg1.transferData(0x01, 0);
      seg1.transferData(0x02, 1);
      seg1.transferData(0x03, 8);
      seg1.transferData(0x04, 7);
      vTaskDelay(INIT_DELAY);
    }
  }
}

void TaskLaserLock(void *pvParameters) {
  (void)pvParameters;

  for (;;) {
    if (stateLaserDetection == ACTIVE) {
      SERIALPRINTS("ACTIVE:\tTaskLaserDetection: \t\n")

      if (!laserDetectionInitialActivation == true) {
        // Show red ring
        for (int i = 0; i < NUM_PIXEL; i++) {
          pixels.SetPixelColor(i, red);
        }
        pixels.Show();
        laserDetectionInitialActivation = true;
      }

      static uint8_t byte_count = 0;

      sequence[byte_count] = digitalRead(detectorPin);

      if (byte_count == SEQUENDE_SIZE) {
        byte_count = 0;
        uint8_t zeros = analyse_sequence(sequence, 0);
        uint8_t ones = analyse_sequence(sequence, 1);

        // chekc if sequenz is correct
        if (zeros == ones && stateLaserDetection == ACTIVE) {
          SERIALPRINTS("Sequence detected ");
          SERIALPRINT("", zeros);
          SERIALPRINTS(" ");
          SERIALPRINT("", ones);
          SERIALPRINTS("\n");
          numberOfSequences++;
          old_time_in_ms = millis();
          // old_time_in_ms = xTaskGetTickCount();
        }
      }

      // check if new additional LED shoulb set to green
      if ((numberOfSequences % 2 == 0) && (numberOfSequences > 0)) {
        uint8_t RGB_led = (uint8_t)numberOfSequences / 2;
        pixels.SetPixelColor(RGB_led, green);  // Moderately bright green color.
        pixels.Show();  // This sends the updated pixel color to the hardware.
      }

      // check if puzzle is solved
      if (numberOfSequences > MAX_SEQUENZES) {
        stateLaserDetection = SOLVED;
        mqttCommunication->publish("7/fusebox/laserDetection", "status",
                                   "solved", true);
        SERIALPRINTS("Fuse Box open\n");
        numberOfSequences = 0;
        blink_ring(5, 2);

        // open LOCK
        digitalWrite(LOCK_0, HIGH);
        vTaskDelay(1000);
        digitalWrite(LOCK_0, LOW);
      }

      // int time_in_ms = xTaskGetTickCount() - old_time_in_ms;
      int time_in_ms = millis() - old_time_in_ms;

      if (time_in_ms >= 500) {
        if (numberOfSequences > 0) {
          if (numberOfSequences % 2 == 0) {
            uint8_t RGB_led = (uint8_t)numberOfSequences / 2;
            pixels.SetPixelColor(RGB_led,
                                 red);  // set led to red
            pixels.Show();
          }
          numberOfSequences--;  // count down sequence if max time was reached
        }
        old_time_in_ms = millis();
        // old_time_in_ms = xTaskGetTickCount();
      }
      byte_count++;
      vTaskDelay(10);
    } else if (stateLaserDetection == SOLVED) {
      SERIALPRINTS("SOLVED:\t\tTaskLaserDetection\n")
      // Show Solution
      for (int i = 0; i < NUM_PIXEL; i++) {
        pixels.SetPixelColor(i, green);
      }
      pixels.Show();
      vTaskDelay(SOLVED_DELAY);
    } else if (stateLaserDetection == INACTIVE) {
      SERIALPRINTS("INACTIVE:\tTaskLaserDetection\n")
      // Show nothing
      for (int i = 0; i < NUM_PIXEL; i++) {
        pixels.SetPixelColor(i, green);
      }
      pixels.Show();
      vTaskDelay(INACTIVE_DELAY);
    } else if (stateLaserDetection == INIT) {
      SERIALPRINTS("INIT:\t\tTaskLaserDetection\n")
      // Show nothing
      for (int i = 0; i < NUM_PIXEL; i++) {
        pixels.SetPixelColor(i, black);
      }
      pixels.Show();
      vTaskDelay(INIT_DELAY);
    }
  }
}

void TaskWiring0Readout(void *pvParameters) {
  (void)pvParameters;
  for (;;) {
    if (stateRewiring0 == ACTIVE) {
      SERIALPRINTS("ACTIVE:\tTaskWiring0Readout: \t\t")
      float rewiringValues0[5];
      uint16_t rewiringPins0[] = {REWIRE_0_1, REWIRE_0_2, REWIRE_0_3,
                                  REWIRE_0_4, REWIRE_0_5};
      for (int i = 0; i <= 4; i++) {
        // read adc, convert and store values in array
        rewiringValues0[i] = analogRead(rewiringPins0[i]);
        rewiringValues0[i] = rewiringValues0[i] / 4095 * 33;
        SERIALPRINT("", i);
        SERIALPRINTS(": ");
        SERIALPRINT("", rewiringValues0[i]);
        SERIALPRINTS(" ");
      }
      // Measured Values: 33 25 19 13 7
      // Problem with [0]: WiFi and ADC not working together,
      // Solution: replaced 13 by 33
      // Check voltages
      if ((rewiringValues0[3] >= 30 && rewiringValues0[3] <= 36) &&
          (rewiringValues0[4] >= 22 && rewiringValues0[4] <= 28) &&
          (rewiringValues0[1] >= 16 && rewiringValues0[1] <= 22) &&
          (rewiringValues0[0] >= 30 && rewiringValues0[0] <= 36) &&
          (rewiringValues0[2] >= 4 && rewiringValues0[2] <= 10)) {
        SERIALPRINTS("Rewiring 0 solved!\n");
        stateRewiring0 = SOLVED;
        mqttCommunication->publish("7/fusebox/rewiring0", "status", "solved",
                                   true);
      } else {
        SERIALPRINTS("Rewiring 0 not solved!\n");
      }
      vTaskDelay(2000);
    } else if (stateRewiring0 == SOLVED) {
      SERIALPRINTS("SOLVED:\t\tTaskWiring0Readout\n")
      vTaskDelay(SOLVED_DELAY);
    } else if (stateRewiring0 == INACTIVE) {
      SERIALPRINTS("INACTIVE:\tTaskWiring0Readout\n")
      vTaskDelay(INACTIVE_DELAY);
    } else if (stateRewiring0 == INIT) {
      SERIALPRINTS("INIT:\t\tTaskWiring0Readout\n")
      vTaskDelay(INIT_DELAY);
    }
  }
}

void TaskWiring1Readout(void *pvParameters) {
  (void)pvParameters;
  for (;;) {
    if (stateRewiring1 == ACTIVE) {
      SERIALPRINTS("ACTIVE:\tTaskWiring1Readout: \t\t")
      // read value from port expander
      uint8_t values = portExpander0.read8();
      // 0x58 + 0x42 = 0x9A = 0b10011010
      // check if value is true
      if (values == 0b10011010) {
        SERIALPRINTS("Rewiring 1 solved!\n")
        stateRewiring1 = SOLVED;
        mqttCommunication->publish("7/fusebox/rewiring1", "status", "solved",
                                   true);
      } else {
        SERIALPRINTS("Rewiring 1 not solved!\n");
        // puzzleStateRewiring1 = UNSOLVED;
      }
      vTaskDelay(2000);
    } else if (stateRewiring1 == SOLVED) {
      SERIALPRINTS("SOLVED:\t\tTaskWiring1Readout\n")
      vTaskDelay(SOLVED_DELAY);
    } else if (stateRewiring1 == INACTIVE) {
      SERIALPRINTS("INACTIVE:\tTaskWiring1Readout\n")
      vTaskDelay(INACTIVE_DELAY);
    } else if (stateRewiring1 == INIT) {
      SERIALPRINTS("INIT:\t\tTaskWiring1Readout\n")
      vTaskDelay(INIT_DELAY);
    }
  }
}

void blink_ring(uint8_t blinking_number, uint8_t frequency) {
  uint16_t period = 1 * 1000 / frequency;
  for (uint8_t k = 0; k < blinking_number; k++) {
    for (int i = 0; i < NUM_PIXEL; i++) {
      // pixels.Color takes RGB values, from 0,0,0 up to 255,255,255
      pixels.SetPixelColor(i, black);  // Moderately bright green color.
      pixels.Show();  // This sends the updated pixel color to the hardware.
    }
    delay(period / 2);
    for (int i = 0; i < NUM_PIXEL; i++) {
      // pixels.Color takes RGB values, from 0,0,0 up to 255,255,255
      pixels.SetPixelColor(i, green);  // Moderately bright green color.
      pixels.Show();  // This sends the updated pixel color to the hardware.
    }
    delay(period / 2);
  }
}

uint8_t analyse_sequence(uint8_t sequence[6], uint8_t target) {
  uint8_t target_number = 0;
  uint8_t len = 6;
  for (int i = 0; i < len; i++) {
    if (sequence[i] == target) {
      target_number++;
    }
  }
  return target_number + 1;
}

void drawOpenPacman(uint8_t xPosition, uint8_t yPosition) {
  // draw Pacman
  ledm1.drawCircle(xPosition, yPosition, 0);
  ledm1.drawCircle(xPosition + 1, yPosition - 1, 0);
  ledm1.drawCircle(xPosition + 2, yPosition - 2, 0);
  ledm1.drawCircle(xPosition + 1, yPosition - 3, 0);
  ledm1.drawCircle(xPosition, yPosition - 3, 0);
  ledm1.drawCircle(xPosition - 1, yPosition - 3, 0);
  ledm1.drawCircle(xPosition - 2, yPosition - 2, 0);
  ledm1.drawCircle(xPosition - 3, yPosition - 1, 0);
  ledm1.drawCircle(xPosition - 3, yPosition, 0);
  ledm1.drawCircle(xPosition - 3, yPosition + 1, 0);
  ledm1.drawCircle(xPosition - 2, yPosition + 2, 0);
  ledm1.drawCircle(xPosition - 1, yPosition + 3, 0);
  ledm1.drawCircle(xPosition - 1, yPosition + 3, 0);
  ledm1.drawCircle(xPosition, yPosition + 3, 0);
  ledm1.drawCircle(xPosition + 1, yPosition + 3, 0);
  ledm1.drawCircle(xPosition + 2, yPosition + 2, 0);
  ledm1.drawCircle(xPosition + 1, yPosition + 1, 0);
}

void drawClosedPacman(uint8_t xPosition, uint8_t yPosition) {
  ledm1.drawCircle(xPosition, yPosition, 3);
}

void drawPointsPacman(uint8_t xPosition, uint8_t yPosition) {
  for (uint8_t i = xPosition + 2; i < 31; i++) {
    if (i % 2 == 0) {
      ledm1.drawCircle(i, yPosition, 0);
    }
  }
}

uint8_t pacmanX = 27;
uint8_t pacmanY = 3;

typedef enum PacmanState { OPEN, CLOSED } tPacmanState;
tPacmanState pacmanState = CLOSED;

void TaskControlPuzzleState(void *pvParameters) {
  (void)pvParameters;
  for (;;) {
    // Check if all puzzles are Solved
    if (statePotentiometer == INACTIVE && stateRewiring0 == INACTIVE &&
        stateRewiring1 == INACTIVE && stateLaserDetection == INACTIVE) {
      ledm1.clear();
      ledm1.drawText(25, 7, "Solved!", MD_MAXPanel::ROT_180);

    } else {
      ledm1.clear();
      if (statePotentiometer == SOLVED || statePotentiometer == INACTIVE) {
        ledm1.drawLine(1, 10, 5, 14);
        ledm1.drawLine(5, 14, 7, 12);
      } else {
        ledm1.drawLine(1, 9, 6, 14);
        ledm1.drawLine(1, 14, 6, 9);
      }
      if (stateRewiring0 == SOLVED || stateRewiring0 == INACTIVE) {
        ledm1.drawLine(9, 10, 13, 14);
        ledm1.drawLine(13, 14, 15, 12);
      } else {
        ledm1.drawLine(9, 9, 14, 14);
        ledm1.drawLine(9, 14, 14, 9);
      }
      if (stateRewiring1 == SOLVED || stateRewiring1 == INACTIVE) {
        ledm1.drawLine(17, 10, 21, 14);
        ledm1.drawLine(21, 14, 23, 12);
      } else {
        ledm1.drawLine(17, 9, 22, 14);
        ledm1.drawLine(17, 14, 22, 9);
      }
      if (stateLaserDetection == SOLVED || stateLaserDetection == INACTIVE) {
        ledm1.drawLine(25, 10, 29, 14);
        ledm1.drawLine(29, 14, 31, 12);
      } else {
        ledm1.drawLine(25, 9, 30, 14);
        ledm1.drawLine(25, 14, 30, 9);
      }

      // PACMAN
      if (pacmanState == tPacmanState::CLOSED) {
        drawOpenPacman(pacmanX, pacmanY);
        pacmanState = tPacmanState::OPEN;
        drawPointsPacman(pacmanX, pacmanY);
      } else if (pacmanState == tPacmanState::OPEN) {
        drawClosedPacman(pacmanX, pacmanY);
        pacmanState = tPacmanState::CLOSED;
      }
      pacmanX++;

      // pacman reached end
      if (pacmanX == 29) {
        pacmanX = 3;
      }
    }

    vTaskDelay(200);
  }
}
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

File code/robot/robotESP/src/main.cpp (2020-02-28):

#include <Arduino.h>
#include <MqttBase.h>
#include <vector>
#include "wifi_secure.h"

#include <string>
#include <sstream>


#define ROBOT_ON 18

/// one pin measures the supply voltage the other the low voltage pin
#define BATTERY_PIN 35
#define BATTERY_LOW 34

float voltage = 0;

bool robot_on = false;

/// communication handling
const char *topic = "7/robot";
const char *mqtt_server = "10.0.0.2";
const char *mqtt_name = "robotClient";
MqttBase *mqtt_com;

/// FreeRTOS functions and handler
void TaskTalk2Robot(void *pvParameters);
void TaskCheckBattery(void *pvParameters);

TaskHandle_t xHandTalk2Robot;
TaskHandle_t xHandleCheckBattery;

/// to_string was not working -> 
template <typename T>
std::string to_string(T value)
{
	std::ostringstream os ;
	os << value ;
	return os.str() ;
}

/// logic callback function for mqtt
void callback(const char *method1, const char *state, int daten) {
  if (caseInSensStringCompare(method1, "TRIGGER")) {
    if (caseInSensStringCompare(state, "on")) {
      robot_on = true;
      std::string str = "robot "+ to_string(voltage);
      mqtt_com->publish(topic, "STATUS", "active", str.c_str(), false);
    }
    if (caseInSensStringCompare(state, "off")) {
      robot_on = false;
      mqtt_com->publish(topic, "STATUS", "inactive", "robot", false);
    }
  }
}

void setup() {
  Serial.begin(115200);

  analogReadResolution(11);
  pinMode(BATTERY_PIN, INPUT);
  pinMode(BATTERY_LOW, INPUT);
  pinMode(ROBOT_ON, OUTPUT);
  /// keep robot off at begining
  digitalWrite(ROBOT_ON, HIGH);

  xTaskCreate(TaskTalk2Robot, "Talk2Robot", 1024, NULL, 2, NULL);

  /// communication intitialization
  std::vector<std::shared_ptr<std::string>> mqtt_topics;
  mqtt_topics.push_back(std::make_shared<std::string>(topic));
  std::vector<std::function<void(const char *, const char *, int)>> logic_callbacks;
  logic_callbacks.push_back(callback);
  mqtt_com = new MqttBase(mqtt_server, mqtt_name, 1883);
  mqtt_com->init(ssid, password, mqtt_topics, logic_callbacks);

  /// FreeRTOS intitialization
  xTaskCreatePinnedToCore(TaskTalk2Robot, "Talk2Robot", 8192, NULL, 3, &xHandTalk2Robot, 0);
  xTaskCreatePinnedToCore(TaskCheckBattery, "CheckBattery", 8192, NULL, 2, &xHandleCheckBattery, 1);
}

void loop() {
  mqtt_com->loop();
  vTaskDelay(500);
}

void TaskTalk2Robot(void *pvParameters) {
  (void)pvParameters;

  for (;;) {
    /// caused by mosfet inverted logic
    if (robot_on == true) {
      digitalWrite(ROBOT_ON, LOW);
    }
    if (robot_on == false) {
      digitalWrite(ROBOT_ON, HIGH);
    }
    vTaskDelay(500);
  }
}

void TaskCheckBattery(void *pvParameters) {
  (void)pvParameters;

  for (;;) {
    /// suspend task to avoid reading interruption
    vTaskSuspend(xHandTalk2Robot);
    uint16_t pinVoltage = 0;
    float batLow = 0;
    for (uint8_t i = 0; i < 5; i++) {
      pinVoltage += analogRead(BATTERY_PIN);
    }
    pinVoltage = (int)pinVoltage / 5;
    voltage = (3.0f/2.0f) * 3.3 * ((float)pinVoltage/2048.0f);
    batLow = analogRead(BATTERY_LOW);
    batLow = 3.3 * ((float)batLow/2048.0f);
    if (batLow > 1.2) {
      std::string str = "robot battery too low : " + to_string(voltage);
      mqtt_com->publish(topic, "STATUS", "failed", str.c_str(), false);
    }
    vTaskResume(xHandTalk2Robot);
    vTaskDelay(3000);
  }
}

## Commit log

2019-11-05 Update README.md
    Added image of room with laser
2019-11-05 Update README.md
    add link to laser sensor
2019-11-07 add pcb design idea
2019-11-07 Update README.md
    Added Description of Stage 2
2019-11-07 add different versions for stage 3
2019-11-14 Added first version of .ino Sketch of ProofOfConcept for fusebox software
2019-11-15 Implemented functionality of buzzers, buttons, freeRTOS and potentiometers. Major Changes in code structure.
2019-11-22 Initial Commit design-fusebox-hardware
    [fusebox.brd, fusebox.sch]
2019-11-22 ignore subfolder for ArduinoOutput
2019-11-26 little changes
    [fusebox.brd]
2019-11-26 update robot and push button
2019-11-26 Added SPI communication with MAX7221
2019-11-26 add basic documentation for FuseBox
2019-11-28 update robot stage
2019-11-28 Added some new functions to schematic and layout
    [fusebox.brd, fusebox.sch]
2019-11-28 fix pinout for esp in fusebox
2019-12-04 RGB Sensor counts the hits of the sensor beam and shows the progress by changing the leds from red to green, counts down if no beam hits the sensor for more than one second. Up and down counting need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
2019-12-05 Major changes, currently problems with task scheduling (Task watchdog triggered. Following tasks did not reset the watchdog in time ..)
    [MAX7221.cpp]
2019-12-05 Added new folder design-software with current software version. Major changes: Removed third party library for MAX72XX, add functionality to custom MAX7221 library. Changed IDE to platform.io
2019-12-05 Changed Serial Logs and removed Debug of WiringPuzzle
2019-12-06 add 3D test file for led ring housing
    [led_ring_cover.stl]
2019-12-06 Added Code fragments of Thomas: LED-Ring and rgbSensor
2019-12-07 add laserLock_Laser_sensor
2019-12-09 implemented down counting of leds
2019-12-09 Added second PCF8574 with some buttons and LEDs, finished I2C circuits, finished MAX7221 circuit, rearranged sheets, minor changes in circuit.
    [fusebox.brd, fusebox.sch]
2019-12-09 split laser and laser sensor
2019-12-12 Some big changes
    [fusebox.brd, fusebox.sch]
2019-12-13 remove .prt file and add -stp instead
    [led_ring_cover.stp]
2019-12-13 add case for pushButton
    [push_button_case_button.stl, push_button_case_button.stp, push_button_case_top.stl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]
2019-12-13 modify push button case
    [push_button_case_button.stl, push_button_case_button.stp, push_button_case_top.stl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]
2019-12-18 Further work on PCB
    [fusebox.brd, fusebox.sch]
2019-12-18 add fuse box 3D files
    [fuse_box_bottom.stp, fuse_box_door.stp, fuse_box_side.stp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]
2019-12-18 Further work on PCB, almost done. Just have to route I2C and SPI lanes.
    [fusebox.brd, fusebox.sch]
2019-12-19 Finished 1st version of layout
    [fusebox.brd]
2019-12-19 added pc mounting holes
    [fusebox.brd]
2019-12-19 change to 2 layer
    [fusebox.brd]
2019-12-19 Implemented Thomis work with the LED Ring and Laser sensor
2019-12-20 minor GND plane fixes
    [fusebox.brd]
2019-12-20 Added Debug LED
2019-12-27 sort 3D files to folder
    [fuse_box_bottom.stp, fuse_box_door.stp, fuse_box_side.stp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]
2019-12-27 add laser case
    [bottom.stl, bottom.stp, laser_lock.stl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]
2020-01-08 add wall mount
    [bottom.stl, bottom.stp, laser_lock.stl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]
2020-01-08 add mounting for LED ring for fuseBox
    [led_ring_mount.stl, led_ring_mount.stp]
2020-01-08 change laserCase to reduced printing time
    [bottom.stl, bottom.stp, top.stl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]
2020-01-08 add fusebox case and laser case
2020-01-09 Changed LED matrix library and some other stuff
2020-01-09 Changed Size of LED Panel: Danke MAXgit add *1git add *1!
2020-01-15 add 3D step and stl files
    [mount_fix.stl, mount_fix.stp, wall_mount.stl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]
2020-01-17 add example for broker(8266) and client
    [broker_esp8266.ino, client_esp32.ino]
2020-01-17 Solution for integer division by zero problem found, not longer using map(..) function!
    [main.cpp]
2020-01-20 wrapper class causes Guru Meditation Error: Core 1 panic'ed
    [main.cpp]
2020-01-20 Corrected Initialization of PubSubClient and WiFiClient
    [main.cpp]
2020-01-20 testing mqtt_bast for laser --> not working right now
    [main.cpp]
2020-01-21 update laser communication
2020-01-21 switch button on an off via mqtt
2020-01-21 switch button on and off oover mqtt, set retain bit if solved, send status active if trigger on is set, send status inactive if trigger off is set
2020-01-21 Serial print changed to Debug
2020-01-21 set duty cycle of laser pin to zero in off state, fixed bug in init of rgb
    [main.cpp]
2020-01-21 revert to previous branch
    [main.cpp]
2020-01-22 make use of pin instead of serial
2020-01-22 Working right now with checking puzzle state from server, sometimes there are still crashes
    [main.cpp]
2020-01-22 New MqttBase, refresh of WiFi at reboot is working now. Software seems stable now. Further improvements are possible, but this status is good for presentation on Friday
    [main.cpp]
2020-01-22 Corrected delays in publish Function
    [main.cpp]
2020-01-23 deleted string lib, deleted print in callback, updated mqtt_base, sends status inactive at startup
2020-01-23 Modified platform.ini of push_button and robotESP, added lib_deps for ArduinoJson and PubSubClient
2020-01-29 add case insensivity
2020-01-29 Added new MqttBase to working fusebox
2020-01-30 Tried to embed pdf of fusebox
2020-01-30 Changed size of schematics
2020-02-04 new mounting files for PS2 controller
    [mount_fix.stl, mount_fix.stp, wall_mount.stl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]
2020-02-04 Changed LED RIng behaviour, changed led matrix behaviour
2020-02-05 more robust design for ps2 mounting
    [mount_fix.stl, mount_fix.stp, wall_mount.stl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]
2020-02-05 Changed Adafruit NeoPixel Library to Neopixel bus library, LED ring is not flickering anymore
2020-02-07 add battery publish
2020-02-08 read out low voltage and ESP power supply
2020-02-14 correct battery status output
    [main.cpp]
2020-02-28 add comments in Button and Laser

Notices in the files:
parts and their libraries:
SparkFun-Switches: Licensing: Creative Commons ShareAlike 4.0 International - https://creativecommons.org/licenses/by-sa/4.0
